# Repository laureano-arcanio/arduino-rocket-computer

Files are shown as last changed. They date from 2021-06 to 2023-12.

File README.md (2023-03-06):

# Arduino Rocket Flight Computer
An Arduino based hardware and software for model rockets recovery and logging system.

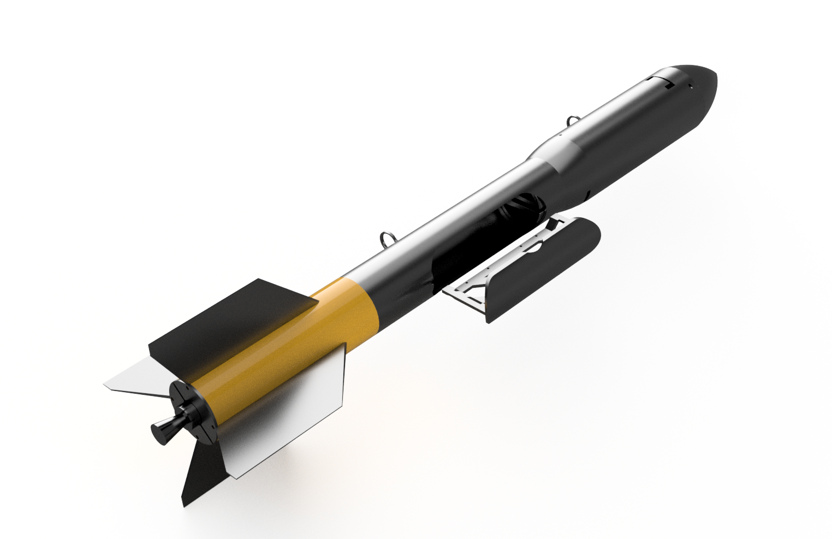
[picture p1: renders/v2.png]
Model 1


## How it works ?
Altitude is measured using a Presion BMP180 Sensor. Data is passed through a Kalman filter and then apogee is detected after 3 consecutive altitude drops.
Logs are stored in a SD card as CSV format, with 1kb redced EEPROM storage as backup (204 rows of 5 bytes).

Parachute deployment is done using a 180º Servo motor

Check out the circuit [here](/schematics/protoboard.png) 

### Full Assembly
Full Assembly

### STL Files
Stl files
All body parts are printed with 1 wall, and 10% infill except for the payload area that needs supports for the servo mount. 

### The Team
The Team

## Check all our FLights and Log [here](https://github.com/laureano-arcanio/arduino-rocket-computer/blob/main/LOGS.md)

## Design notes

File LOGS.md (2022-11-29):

## Saturday, October 15th 2022 18:04pm
### First Rocket Flight
- **Date:** Saturday, October 15th 2022 18:04pm
- **Rocket version:** v46
- **Computer firmware:** Commit 24 #9e297cbeb49c01d56837683099e77f7d58b3c18b
- **Engine:** 18g KNSU (water re-cristalinization)
- **Status:** Partial success, rocket recovered safe. Data logs not stored

**Logs:**

Our first flight deployed parachute before apogee, due to an issue with flight computer executing Emergency mode right after liftoff. Anyways, we recovered the entire rocket without any damage.
[First Flight](https://www.youtube.com/watch?v=o5odCazfV4E)

## Saturday, October 15th 2022 18:04pm
### Second Rocket Flight
Same as before

## October 16th 2022 18:04pm
### Third Rocket Flight (Cancelled)
- **Date:** Sunday, October 16th 2022 18:04pm
- **Rocket version:** v46
- **Computer firmware:** Commit 24 #9e297cbeb49c01d56837683099e77f7d58b3c18b
- **Engine:** 18g KNSU (water re-cristalinization)
- **Status:** Cancelled due to low battery and wiring issue.

**Logs:**

Our battery compleately died. We struggle with some bad wiring for a long time beferohand. 

## Saturday, October 29th 2022 20:15pm
### Fourth Rocket flight
- **Date:** Saturday, October 29th 2022 20:15pm
- **Rocket version:** v48
- **Computer firmware:** Commit 38 ec74b0bc3eabf66b300b1d60ef9739c1b33f2775
- **Engine:** 18g KNSU (water re-cristalinization)
- **Status:** Failure. Engine failure, Computer failure. 

**Logs:**

We experienced several unknown issues, initially servo lock did not work. This overheated the servo and some wires burnt out. After several attemps, we manage to get computer to ready status, fired the rocket but engine failes at about 5-7 mts hight. Rocket recovered almost 100% safe except for a broken finn. None logs where stored, we figured out 180deg servos don't work well on edges. so we switched from 0 to 25 deg to 15 to 40.

## Wednesday, November 9 2022 17hs
### Fifth Rocket Flight
- **Date:** Wednesday, November 9 2022 17hs
- **Weather**: Sunny, Windy (10-15knots)
- **Rocket version:** v48
- **Computer firmware:** Commit 44 58a310a3b09a8df3bc02ff4712aa3345adc88105
- **Engine:** 18g KNSU (Nakka method, caramelization of fine powder grains)
- **Status:** Failure. Computer failure. Avionics totally destroyed, computer, parachute and engine recovered

**Logs:**

Our rocket flow perfectly, but parachute did not ejected. After landing, and some further investigation we figured out for some reason the computer switched to Liftoff status before liftoff (probably due to pression change, was a windy day). And due to launchpad conditions switched to landed after 3.5s. So the rocket flown with a computer in Landed status. We'll fix the liftoff condition to account for more meters (>5) and shorten EMERGENCY deploy time to fit this rocket motor. (4s)
[Fifth Flight](https://www.youtube.com/watch?v=9i5LRDVh-5M)

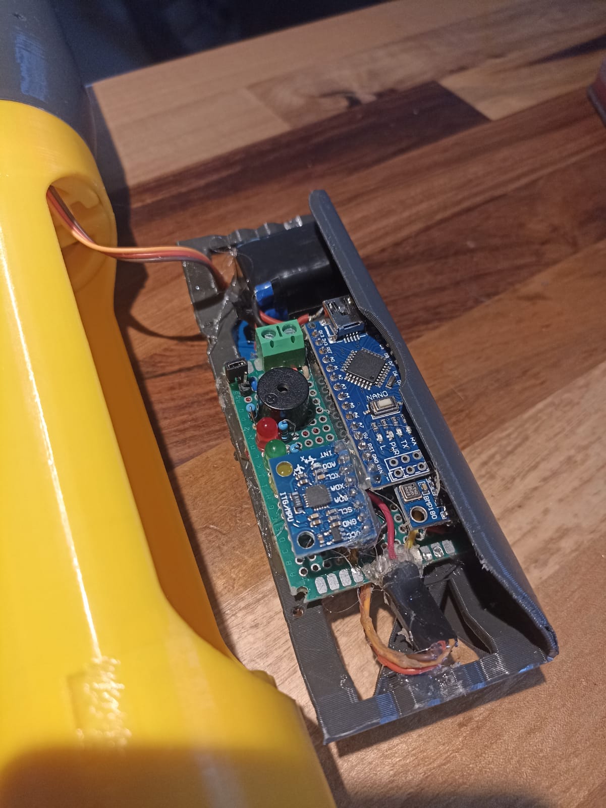
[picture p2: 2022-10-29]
images/Electronics_v1.jpeg

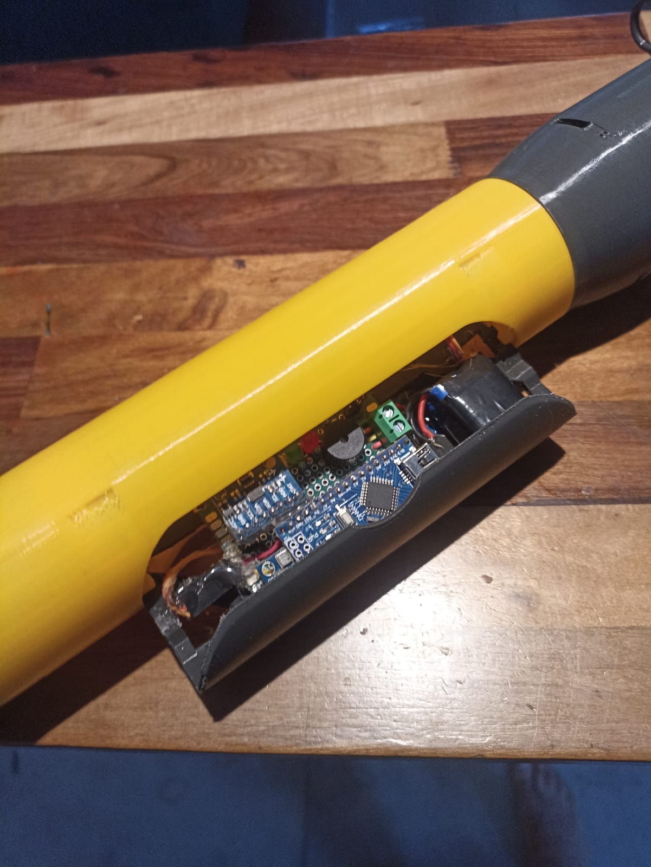
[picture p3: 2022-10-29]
images/Electronics_bay_v2.jpeg

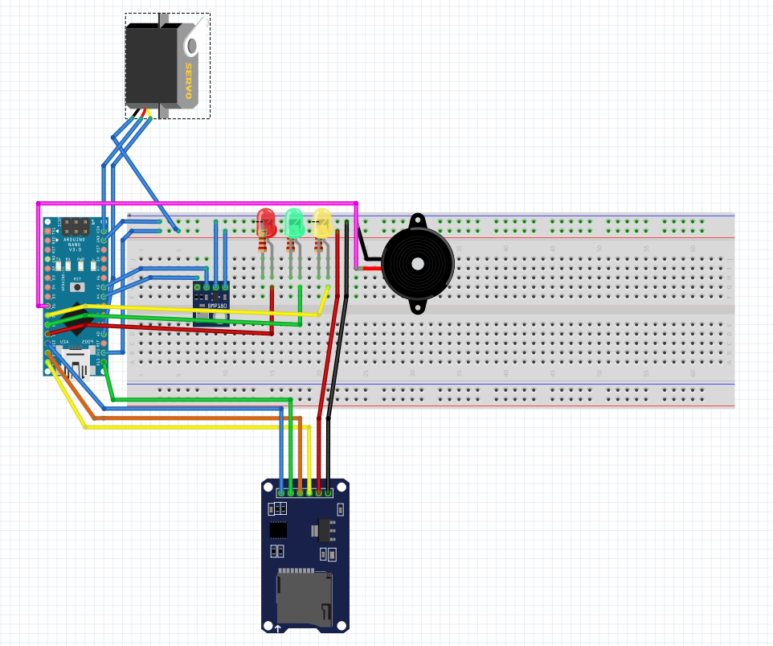
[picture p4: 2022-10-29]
schematics/protoboard.png

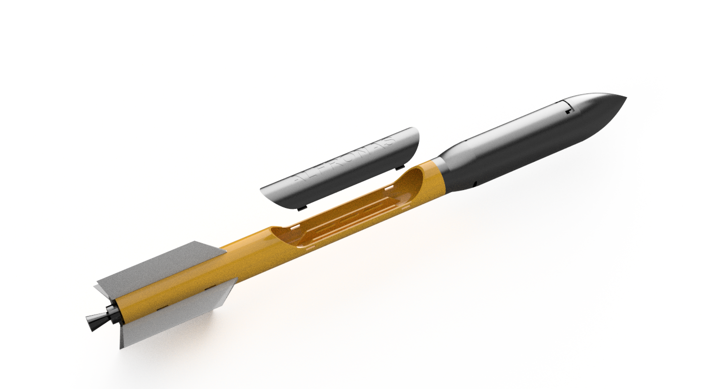
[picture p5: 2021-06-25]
renders/v1.png

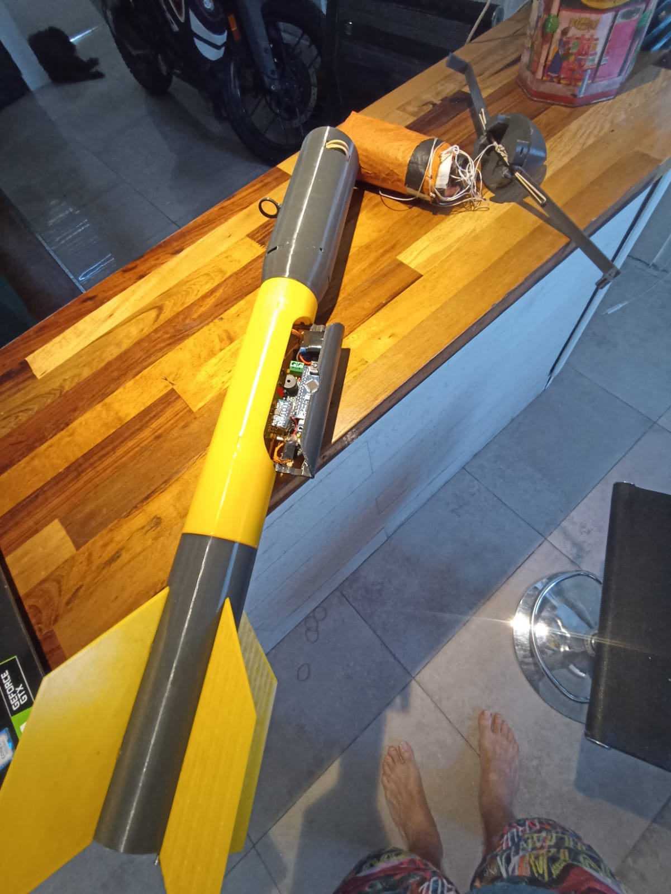
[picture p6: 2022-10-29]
images/Full_chute_deploy_v2.jpeg

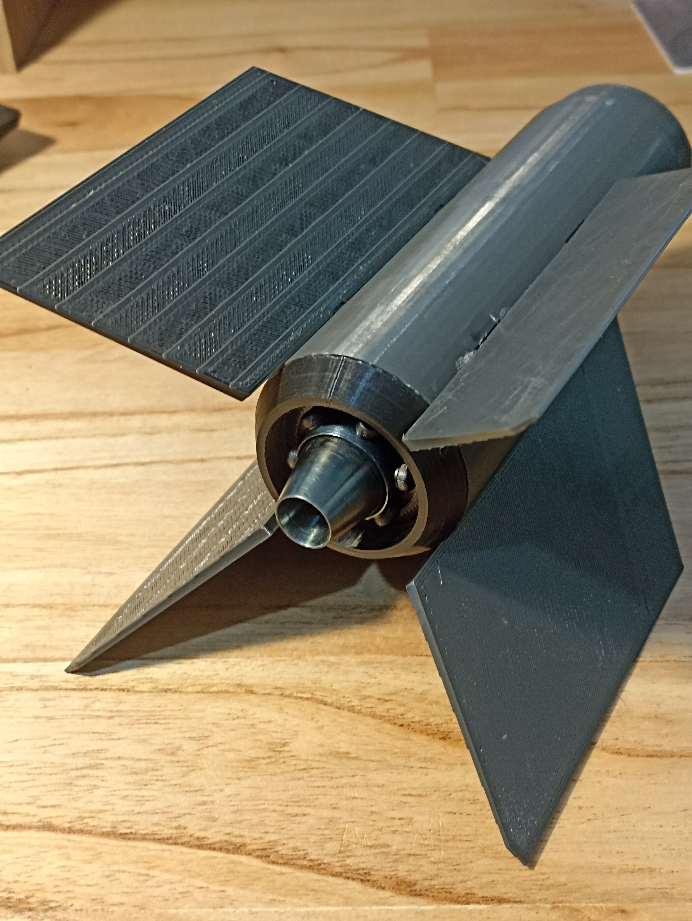
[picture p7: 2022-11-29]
images/E motor mounted.jpg

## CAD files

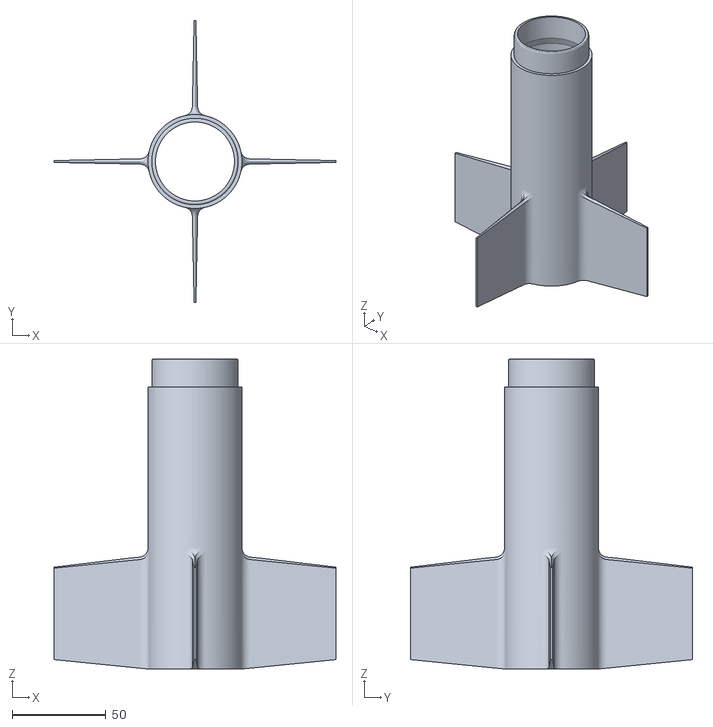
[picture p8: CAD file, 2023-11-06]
STLs/body_motor_section.stl
149.9 x 149.9 x 165.0

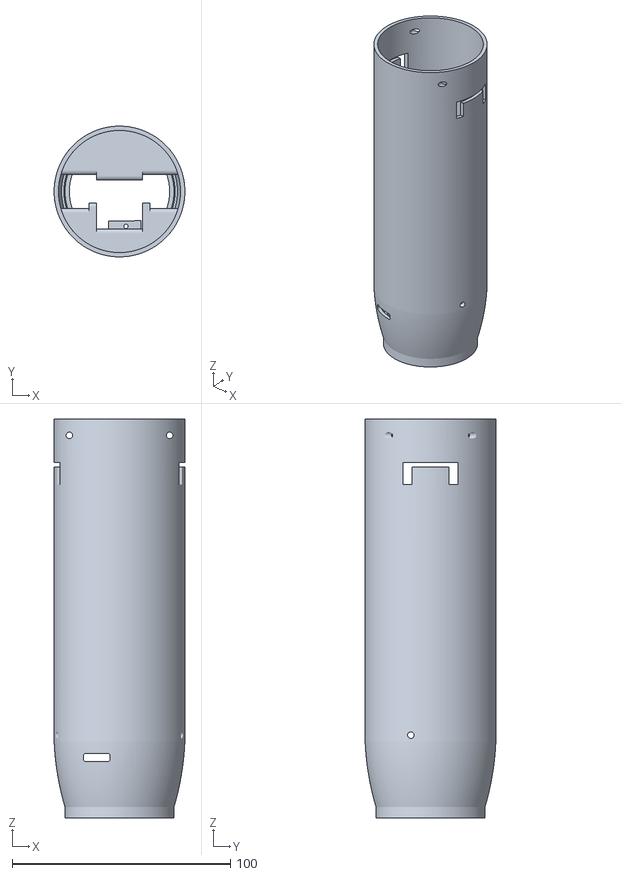
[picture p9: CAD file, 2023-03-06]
STLs/body_payload_area.stl
60.0 x 60.0 x 183.0

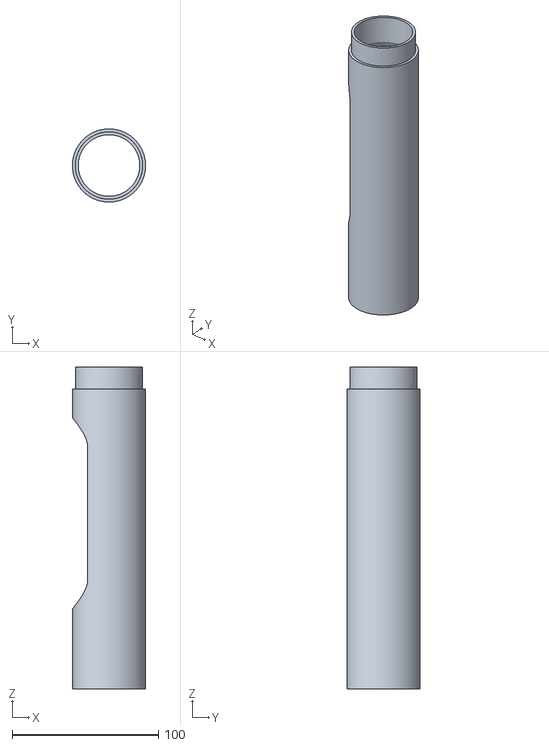
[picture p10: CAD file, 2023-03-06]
STLs/body_electronics_munt.stl
50.0 x 50.0 x 220.0

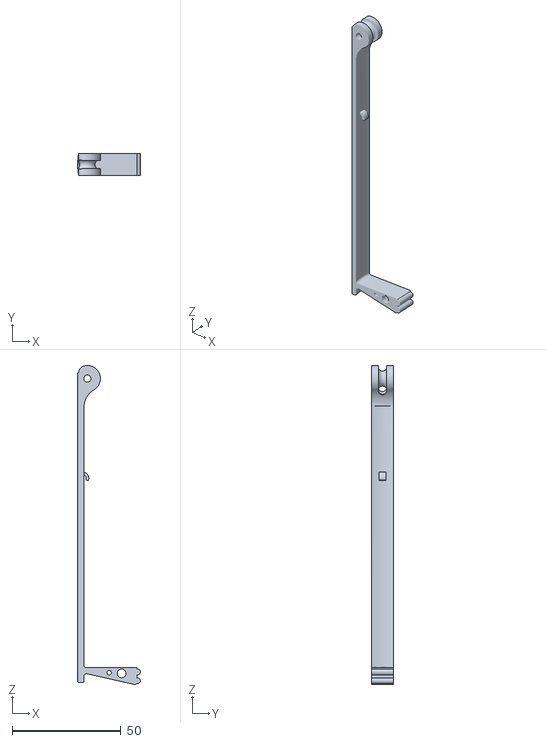
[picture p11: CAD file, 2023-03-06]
STLs/payload_release_arm_left.stl
28.9 x 10.0 x 146.4

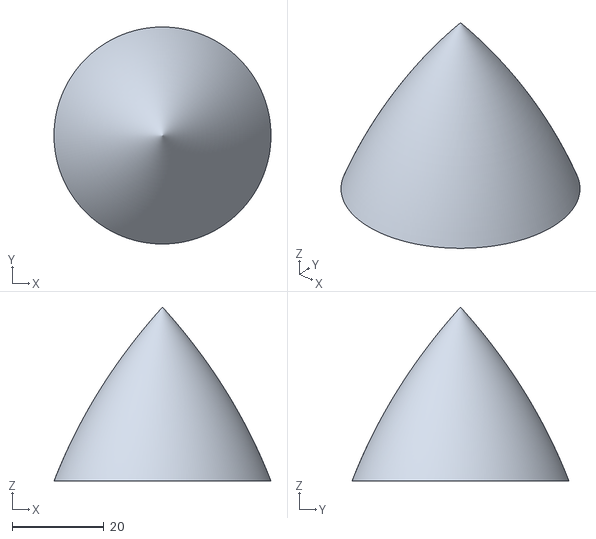
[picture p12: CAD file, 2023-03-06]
STLs/payload_release_nose_top.stl
47.4 x 47.4 x 38.0

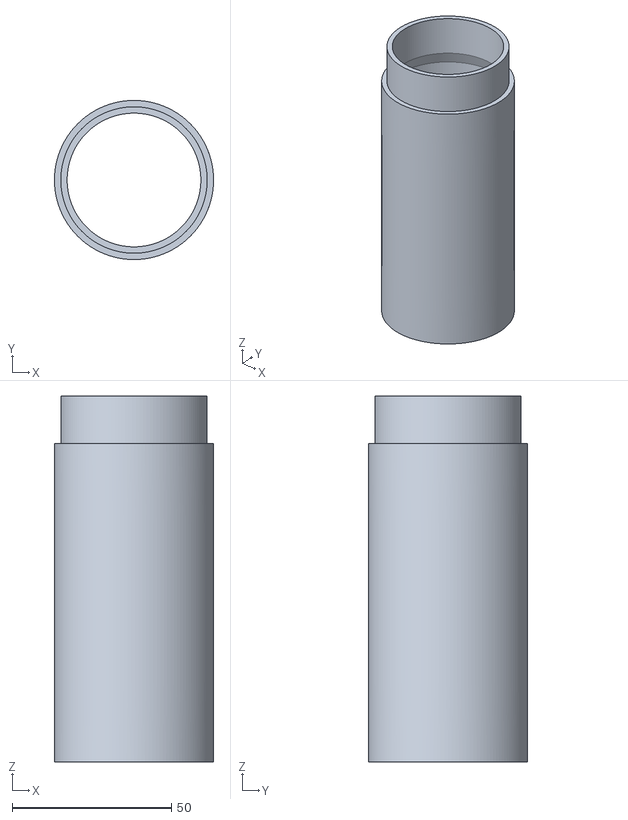
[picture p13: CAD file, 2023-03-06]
STLs/body_extension.stl
50.0 x 50.0 x 115.0

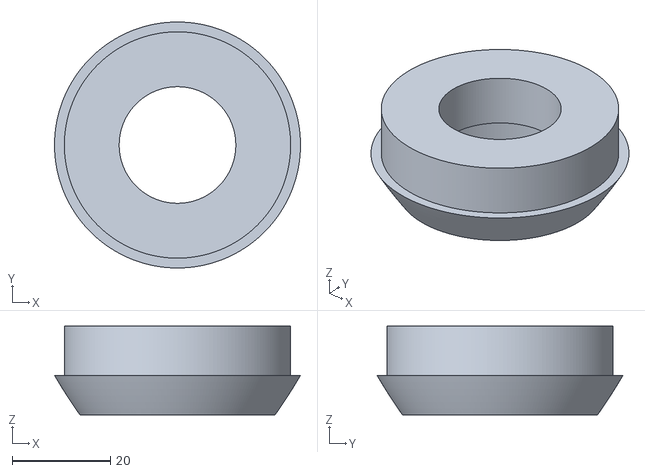
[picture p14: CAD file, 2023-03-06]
STLs/abs_motor_mount.stl
50.0 x 50.0 x 18.0

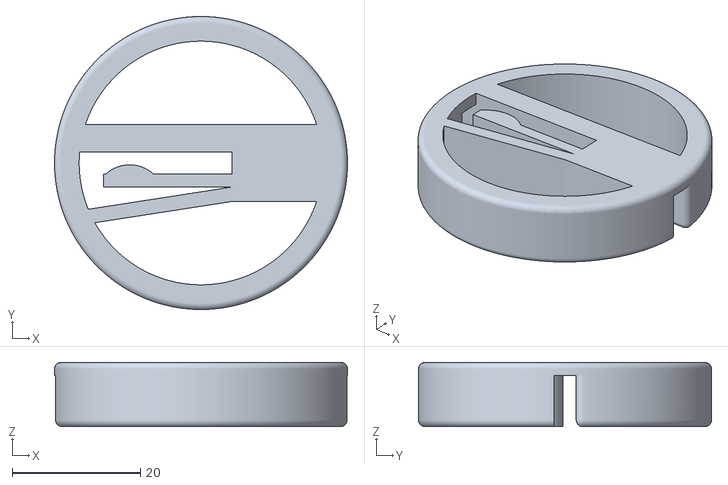
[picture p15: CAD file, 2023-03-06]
STLs/electronics_rack_guide_top.stl
45.7 x 45.7 x 10.0

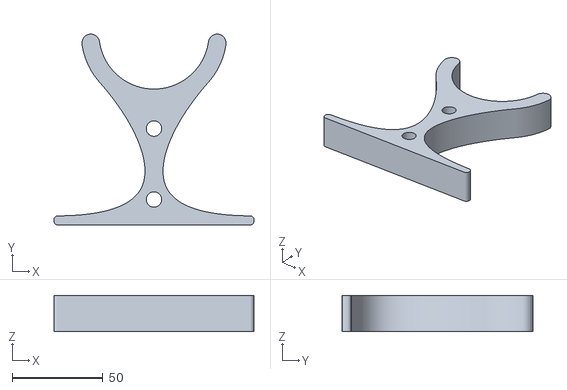
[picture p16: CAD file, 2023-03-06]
STLs/rocket_stand_base.stl
110.0 x 105.0 x 20.0

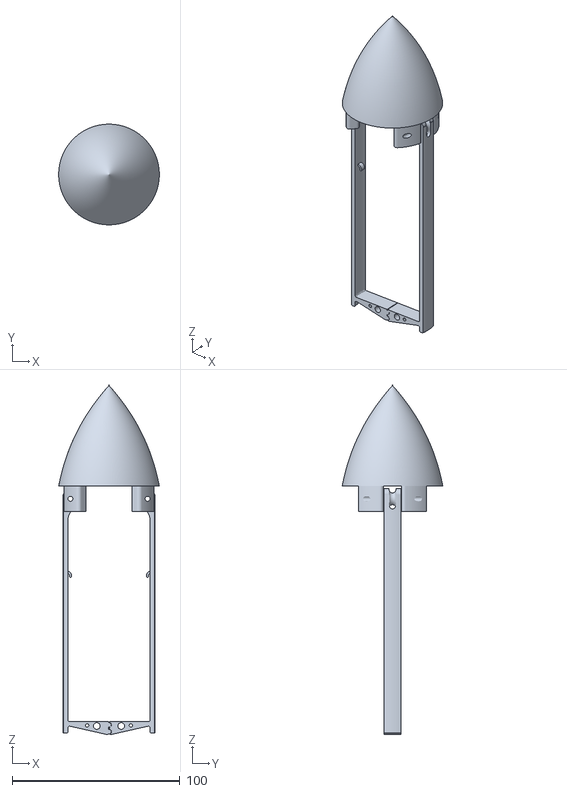
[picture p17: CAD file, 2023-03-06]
STLs/payload_release_arm_right.stl
60.0 x 60.0 x 207.9

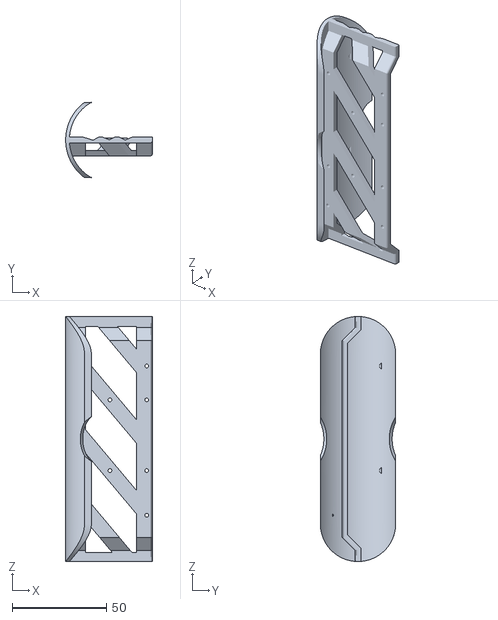
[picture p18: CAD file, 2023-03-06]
STLs/electronics_rack.stl
46.0 x 40.0 x 130.0

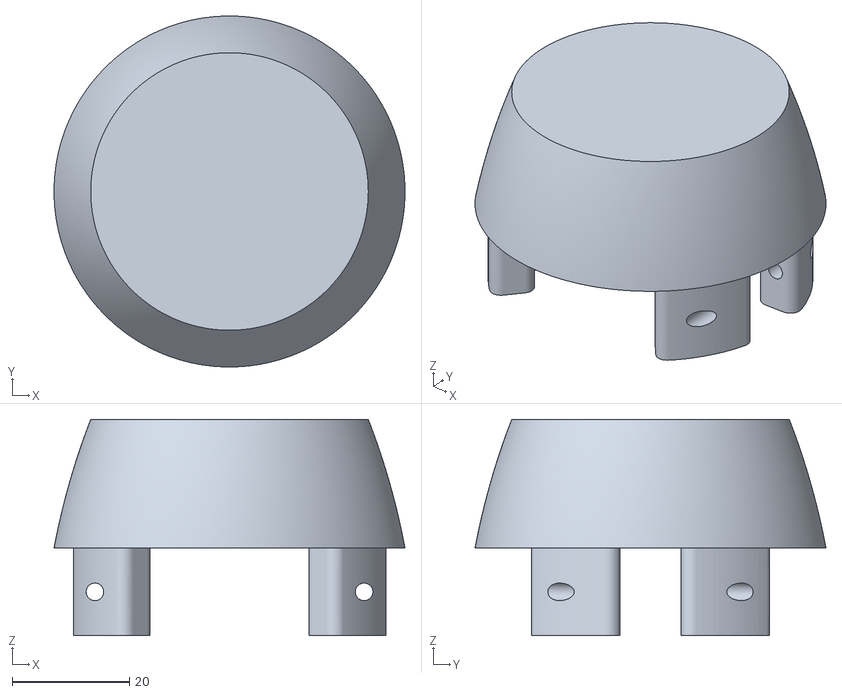
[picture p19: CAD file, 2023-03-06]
STLs/payload_release_nose_base.stl
60.0 x 60.0 x 37.0

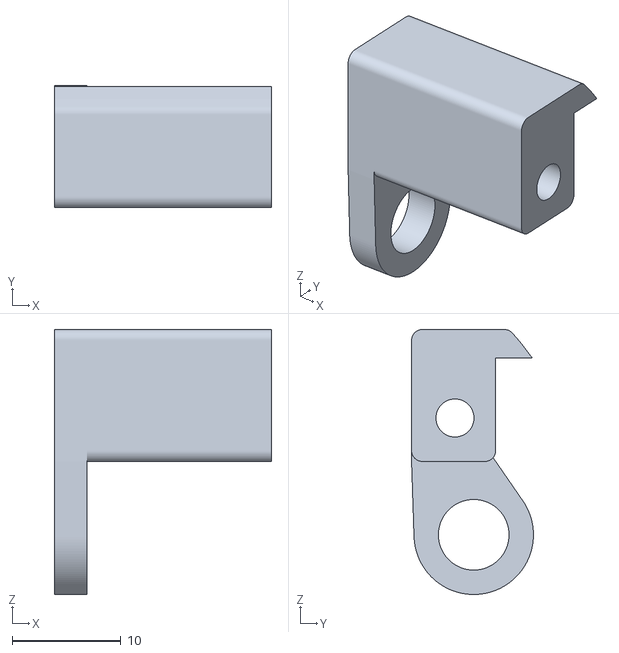
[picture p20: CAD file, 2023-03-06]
STLs/payload_release_pin.stl
20.0 x 11.2 x 24.4

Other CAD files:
STLs/electronics_rack_guide_bottom.stl

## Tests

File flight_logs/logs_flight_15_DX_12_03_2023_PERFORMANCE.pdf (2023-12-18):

## Rocket Flight Analisys

Rocket Mass): 0.41 kg
Max altitude: 250 Mts
Time at max altitude: 7.29 s Max Speed: 85.73 mts/s
Time at max speed: 1.07 s
Power flight time (s): 1.03 s
Max Acceleration: 167.3 mts/s^2 Time at max acceleration: 0.0 s Total Impulse: 35.2 Ns
Average descent speed: -9.57 mts/s

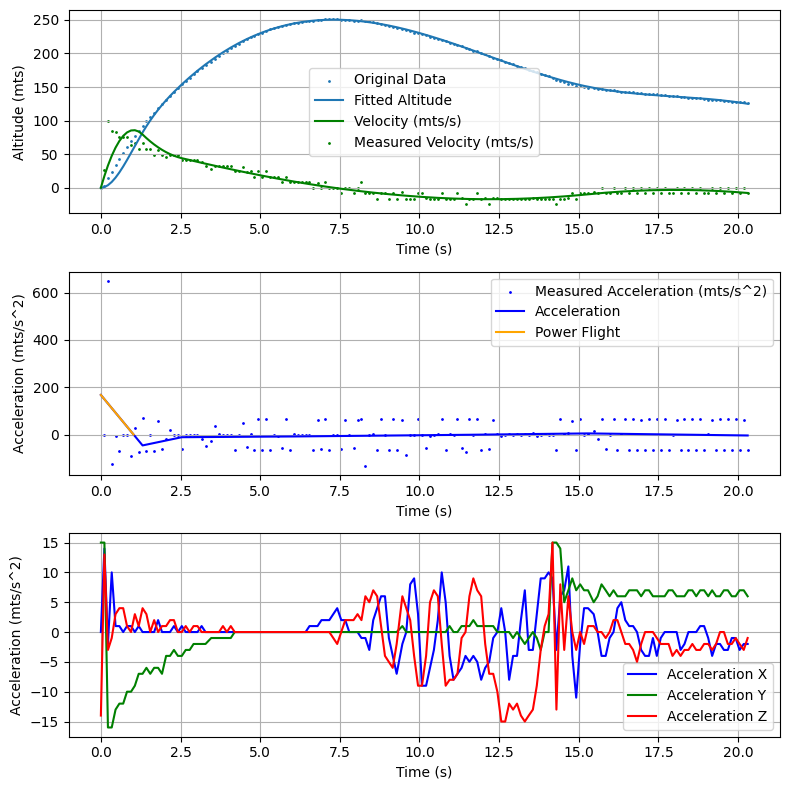
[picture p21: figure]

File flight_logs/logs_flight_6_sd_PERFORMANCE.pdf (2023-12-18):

## Rocket Flight Analisys

Rocket Mass): 0.41 kg
Max altitude: 42 Mts
Time at max altitude: 3.16 s Max Speed: 20.34 mts/s
Time at max speed: 1.55 s
Power flight time (s): 1.52 s
Max Acceleration: 26.77 mts/s^2 Time at max acceleration: 0.0 s Total Impulse: 8.34 Ns
Average descent speed: -2.38 mts/s

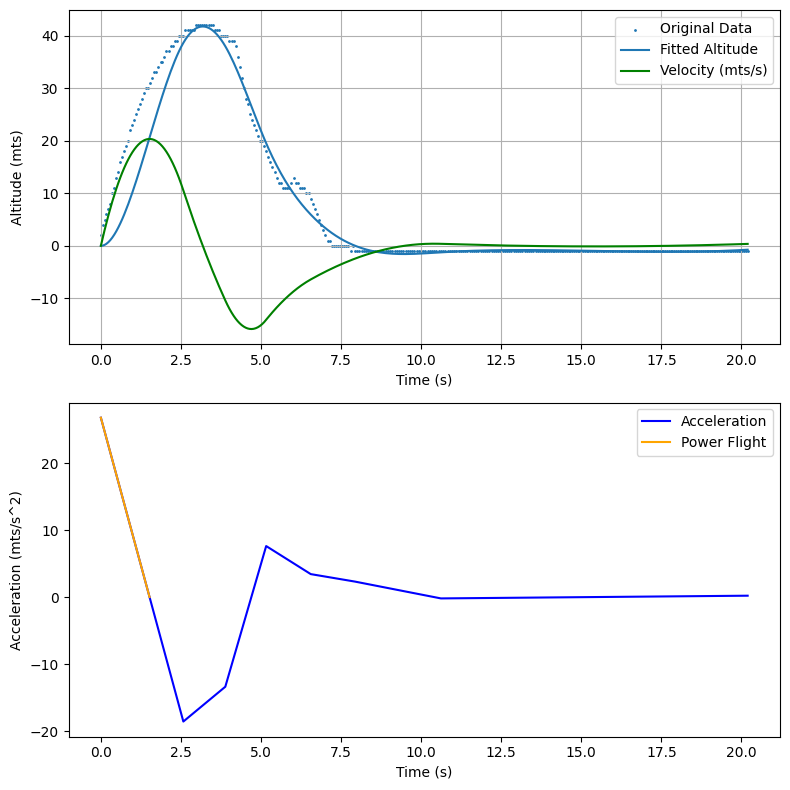
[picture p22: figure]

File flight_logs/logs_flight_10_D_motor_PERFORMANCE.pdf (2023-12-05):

## Rocket Flight Analisys

Rocket Mass): 0.41 kg
Max altitude: 137 Mts
Time at max altitude: 5.76 s Max Speed: 37.05 mts/s
Time at max speed: 2.8 s
Power flight time (s): 2.75 s
Max Acceleration: 26.96 mts/s^2 Time at max acceleration: 0.0 s Total Impulse: 15.2 Ns
Average descent speed: -4.56 mts/s

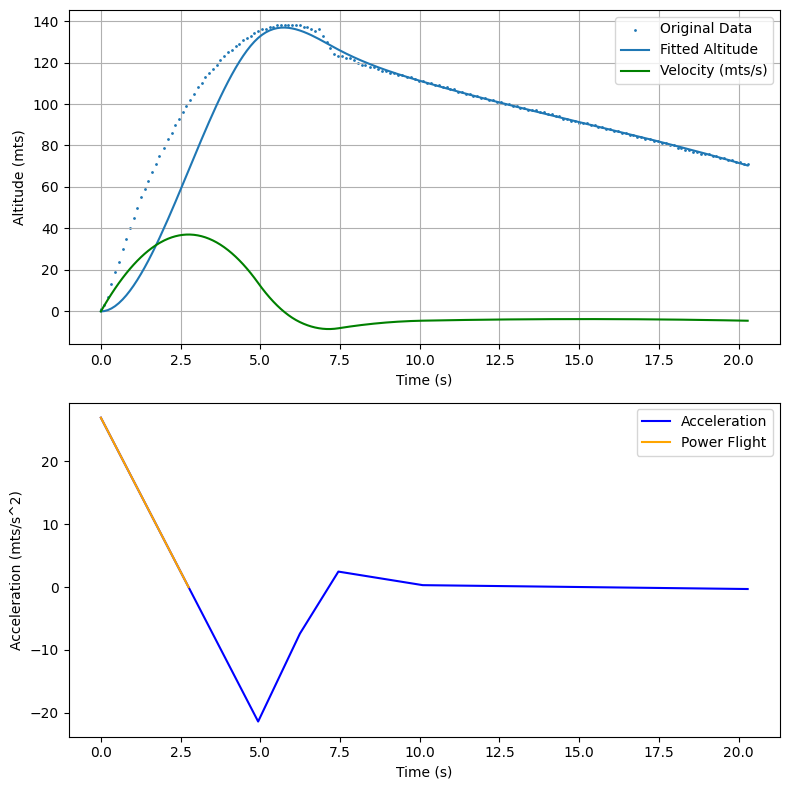
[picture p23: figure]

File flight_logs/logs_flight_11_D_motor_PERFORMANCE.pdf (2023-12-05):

## Rocket Flight Analisys

Rocket Mass): 0.41 kg
Max altitude: 139 Mts
Time at max altitude: 9.13 s Max Speed: 58.77 mts/s
Time at max speed: 0.81 s
Power flight time (s): 0.76 s
Max Acceleration: 161.53 mts/s^2 Time at max acceleration: 0.0 s Total Impulse: 24.15 Ns
Average descent speed: -6.49 mts/s

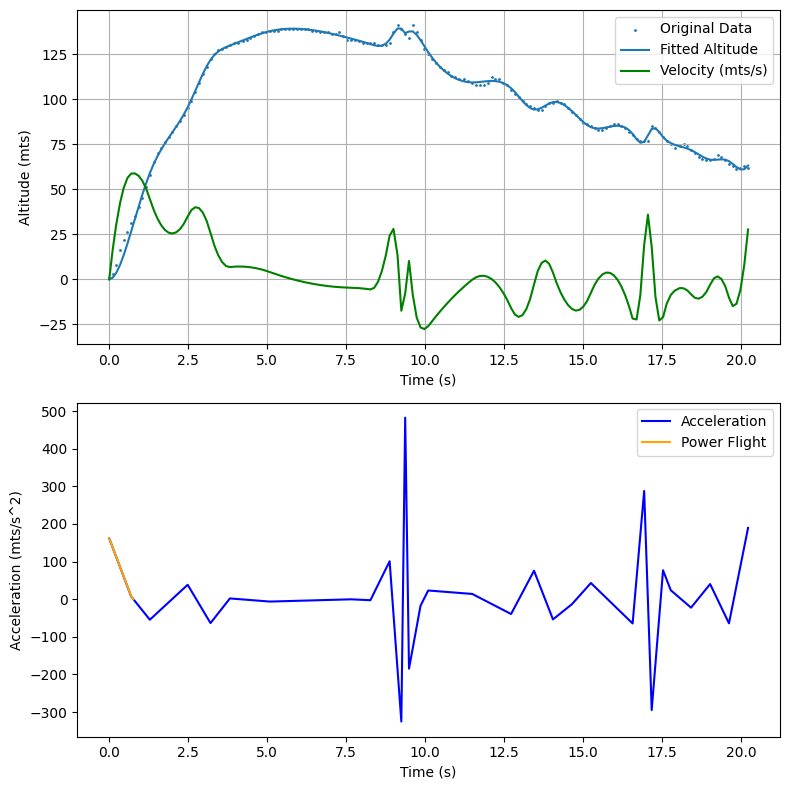
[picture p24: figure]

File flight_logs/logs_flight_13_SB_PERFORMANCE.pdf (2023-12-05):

## Rocket Flicht Analisys

Rocket Mass): 0.41 kg
Max altitude: 177 Mts
Time at max altitude: 6.43 s Max Speed: 67.89 mts/s
Time at max speed: 0.49 s
Power flight time (s): 0.47 s
Max Acceleration: 292.23 mts/s^2 Time at max acceleration: 0.0 s Total Impulse: 27.89 Ns
Average descent speed: -4.19 mts/s

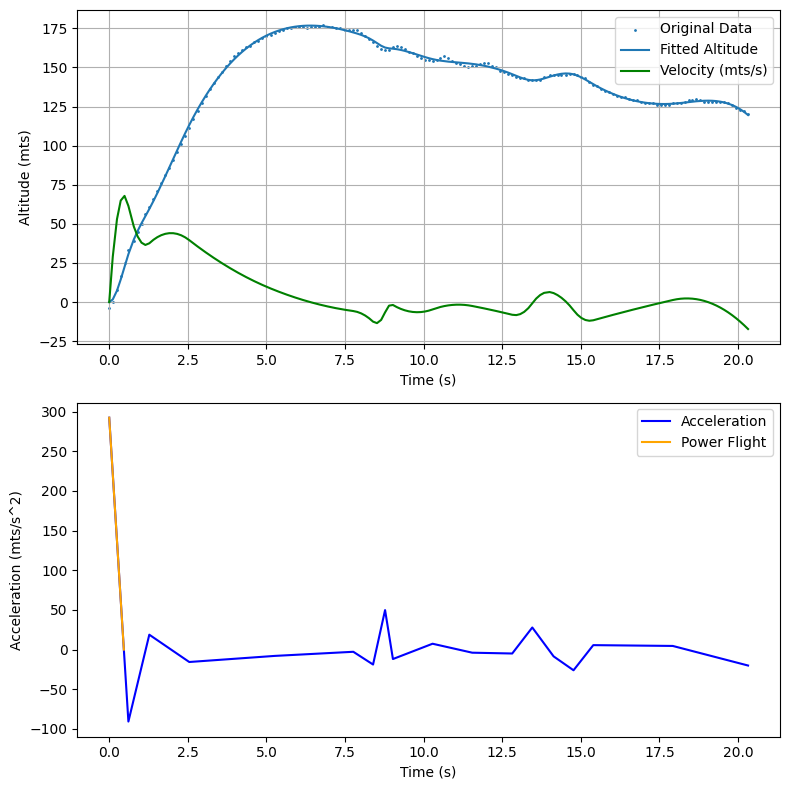
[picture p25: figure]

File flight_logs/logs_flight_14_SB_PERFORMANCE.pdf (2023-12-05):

## Rocket Flicht Analisys

Rocket Mass): 0.41 kg
Max altitude: 193 Mts
Time at max altitude: 6.58 s Max Speed: 56.46 mts/s
Time at max speed: 1.88 s
Power flight time (s): 1.9 s
Max Acceleration: 59.37 mts/s^2 Time at max acceleration: 0.0 s Total Impulse: 23.15 Ns
Average descent speed: -4.02 mts/s

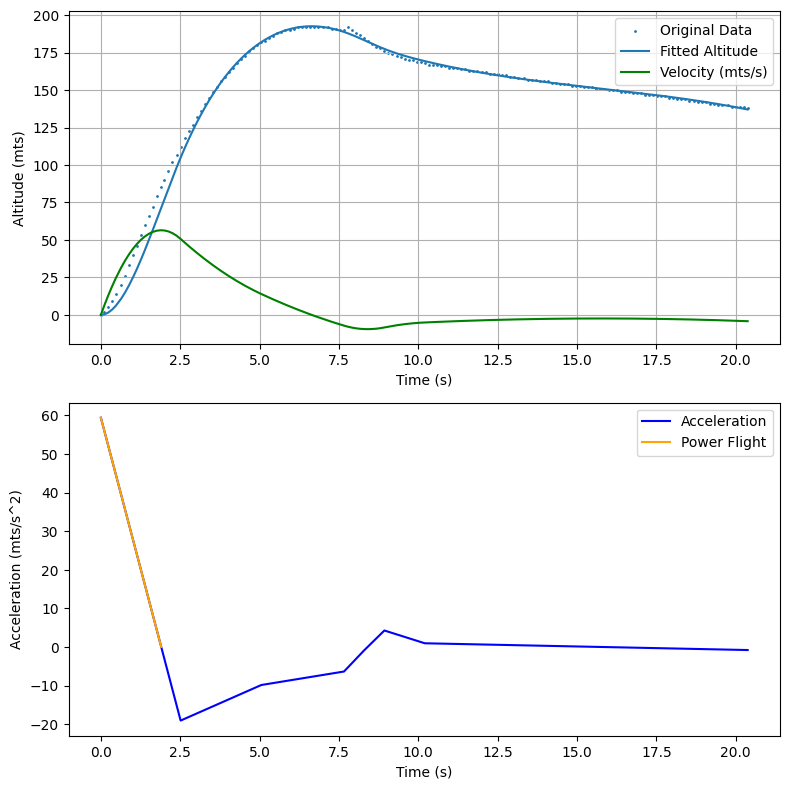
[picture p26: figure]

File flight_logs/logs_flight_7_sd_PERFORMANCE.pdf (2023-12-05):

## Rocket Flight Analisys

Rocket Mass): 0.41 kg
Max altitude: 32 Mts
Time at max altitude: 2.9 s Max Speed: 16.85 mts/s
Time at max speed: 1.4 s
Power flight time (s): 1.42 s
Max Acceleration: 23.78 mts/s^2 Time at max acceleration: 0.0 s Total Impulse: 6.91 Ns
Average descent speed: -1.78 mts/s

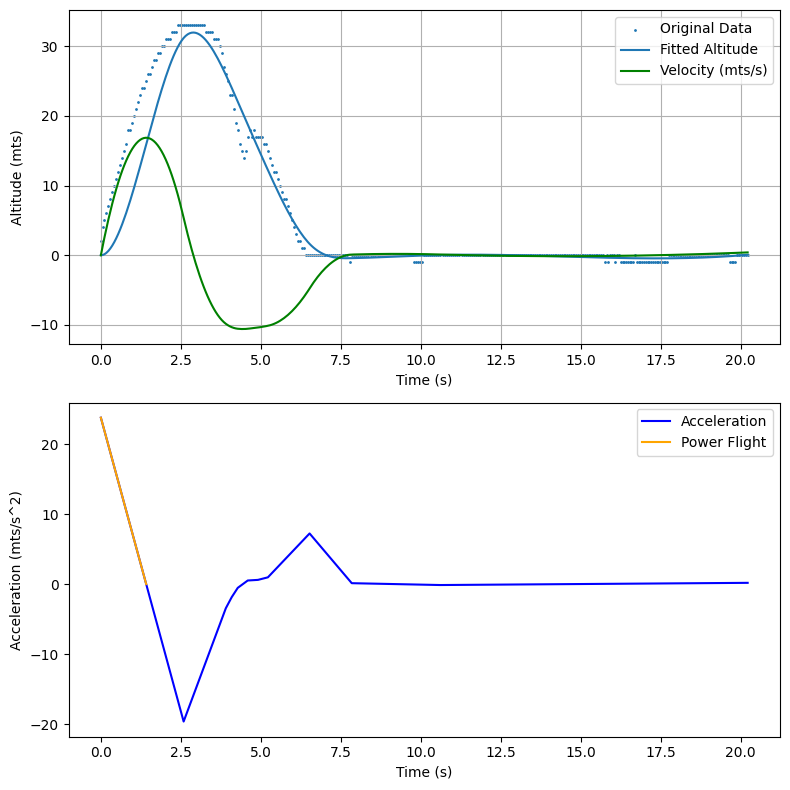
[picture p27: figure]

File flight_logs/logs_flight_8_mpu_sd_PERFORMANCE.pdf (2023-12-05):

## Rocket Flight Analisys

Rocket Mass): 0.41 kg
Max altitude: 44 Mts
Time at max altitude: 3.36 s Max Speed: 20.17 mts/s
Time at max speed: 1.61 s
Power flight time (s): 1.63 s Max Acceleration: 24.7 mts/s^2 Time at max acceleration: 0.0 s Total Impulse: 8.27 Ns
Average descent speed: -2.47 mts/s

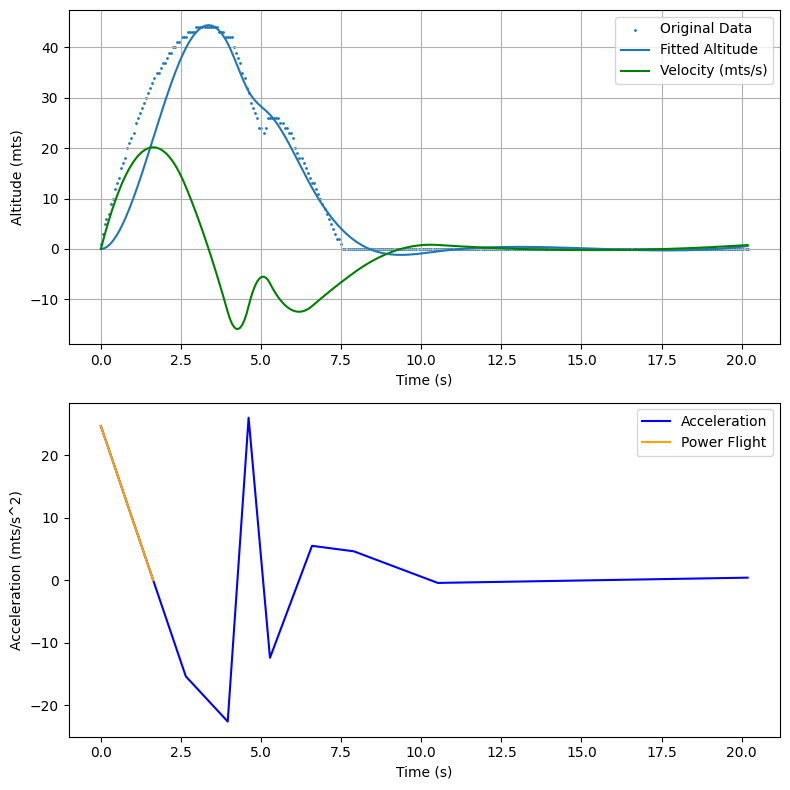
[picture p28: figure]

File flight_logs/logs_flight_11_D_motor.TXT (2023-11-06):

Ms	Code	A0	CA	MA	T	AX	AY	AZ	GX	GY	GZ
0	20	0.00	0	0.60	29.20	0	-8	0	-136	-821	-6	
106	20	0.00	0	1.83	29.20	0	-7	0	-302	-15	-12	
210	20	0.00	1	1.39	29.20	0	-7	0	-268	-554	27	
317	20	0.00	1	1.22	29.20	0	-7	0	-178	-293	-111	
422	20	0.00	1	1.48	29.20	0	-8	0	-177	-308	-31	
529	20	0.00	1	1.30	29.20	0	-8	0	-276	-439	13	
635	20	0.00	1	1.13	29.30	0	-8	0	-285	-522	-37	
748	20	0.00	1	1.48	29.30	0	-7	0	-296	167	105	
852	20	0.00	1	2.00	29.20	0	-8	0	-120	-714	-183	
959	20	0.00	1	1.83	29.20	0	-8	0	-347	-35	136	
1064	20	0.00	1	1.30	29.20	0	-8	0	-264	609	177	
1172	20	0.00	1	2.17	29.20	0	-8	0	-236	-327	-156	
1279	20	0.00	1	1.74	29.30	0	-8	0	-411	-593	-80	
1386	20	0.00	1	1.91	29.30	0	-7	0	-297	-488	-83	
1493	20	0.00	1	2.17	29.30	0	-8	-1	-358	-2049	78	
1600	20	0.00	1	1.74	29.30	0	-7	0	-452	-249	-67	
1707	20	0.00	1	2.00	29.30	0	-8	0	-152	-352	-10	
1815	20	0.00	1	1.65	29.30	0	-8	0	-121	-197	-163	
1928	20	0.00	1	1.56	29.30	0	-8	0	-367	-662	-70	
2034	20	0.00	1	2.00	29.30	0	-8	0	-274	70	127	
2141	20	0.00	1	1.74	29.30	0	-8	0	-210	-147	84	
2249	20	0.00	1	1.65	29.30	0	-8	0	-346	-605	-160	
2355	20	0.00	1	2.52	29.30	0	-8	0	-193	-268	-139	
2463	20	0.00	1	1.48	29.30	0	-7	0	-235	-156	96	
2569	20	0.00	1	1.65	29.30	0	-8	0	-326	-138	-29	
2677	20	0.00	1	1.91	29.30	0	-8	0	-324	-514	-146	
2784	20	0.00	1	1.91	29.30	0	-8	0	-46	-321	-78	
2891	20	0.00	1	1.13	29.30	0	-8	0	-226	-408	131	
2999	20	0.00	1	1.74	29.30	0	-8	0	-437	-132	67	
3112	20	0.00	1	1.22	29.30	0	-8	0	-175	-295	-111	
3219	20	0.00	1	1.74	29.30	0	-7	0	-226	19	-75	
3325	20	0.00	1	1.13	29.30	0	-8	0	-393	53	196	
3433	20	0.00	1	1.65	29.30	0	-8	0	-375	228	166	
3539	20	0.00	1	1.30	29.30	0	-8	0	-152	-406	-128	
3647	20	0.00	1	1.48	29.30	0	-8	0	-256	-511	-208	
3754	20	0.00	1	1.39	29.30	0	-7	0	-296	-315	3	
3861	20	0.00	1	1.83	29.30	0	-8	0	-202	75	110	
3968	20	0.00	1	1.39	29.30	0	-8	0	-284	-179	-25	
4076	20	0.00	1	1.22	29.30	0	-8	0	-342	-56	-94	
4182	20	0.00	1	0.34	29.40	-1	-8	0	-220	-160	119	
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

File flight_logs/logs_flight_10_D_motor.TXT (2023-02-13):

Ms	Code	A0	CA	MA	T	AX	AY	AZ	GX	GY	GZ
0	20	0.00	0	-0.51	27.40	0	-8	0	-486	-1151	92	
123	20	0.00	0	-0.25	27.40	0	-8	0	-263	-312	7	
227	20	0.00	0	-0.25	27.50	0	-8	0	-243	-194	26	
334	20	0.00	0	-0.16	27.50	0	-8	0	-286	17	-38	
441	20	0.00	0	-0.25	27.50	0	-8	0	-238	-25	11	
548	20	0.00	0	0.11	27.50	0	-8	0	-132	511	47	
655	20	0.00	0	0.02	27.50	-1	-4	0	-148	1356	-66	
760	20	0.00	0	-0.07	27.50	0	-8	0	-159	-217	33	
867	20	0.00	0	0.20	27.50	0	-8	0	-52	1188	-238	
973	20	0.00	0	-0.51	27.50	0	-8	0	7	-1045	-80	
1081	20	0.00	0	0.54	27.50	0	-8	0	-321	-392	8	
1194	20	0.00	0	-0.16	27.50	0	-8	0	-549	3642	16	
1299	20	0.00	0	0.28	27.50	0	-8	0	-224	1180	-180	
1406	20	0.00	0	-0.33	27.50	0	-7	0	-138	-217	-32	
1514	20	0.00	0	-0.60	27.50	0	-8	0	-419	351	58	
1622	20	0.00	0	-0.16	27.50	0	-8	0	-272	-323	-40	
1731	20	0.00	0	-0.07	27.50	0	-8	0	-106	-565	-34	
1838	20	0.00	0	-0.42	27.50	0	-8	0	-229	-208	26	
1947	20	0.00	0	-0.42	27.50	0	-8	0	-432	131	-16	
2056	20	0.00	0	-0.16	27.50	0	-8	0	-225	-305	-37	
2163	20	0.00	0	-0.42	27.50	0	-8	0	-87	-578	10	
2278	20	0.00	0	0.11	27.50	0	-8	0	-264	-87	-18	
2382	20	0.00	0	0.11	27.50	0	-8	0	-361	30	-45	
2489	20	0.00	0	-0.25	27.50	0	-8	0	-175	-401	27	
2597	20	0.00	0	0.11	27.50	0	-8	0	-152	-467	-32	
2704	20	0.00	0	0.20	27.50	0	-7	0	-301	-172	-24	
2811	20	0.00	0	-0.51	27.50	0	-8	0	-348	-109	14	
2920	20	0.00	0	-0.42	27.50	0	-8	0	-159	-469	-24	
3027	20	0.00	0	-0.25	27.50	0	-8	0	-177	-454	-18	
3136	20	0.00	0	-0.16	27.50	0	-8	0	-345	-114	0	
3243	20	0.00	0	-0.16	27.50	0	-8	0	-295	-165	-23	
3353	20	0.00	0	-0.33	27.50	0	-8	0	-115	-492	-22	
3503	20	0.00	0	0.20	27.50	0	-8	0	-313	-166	-22	
3608	20	0.00	0	-0.07	27.50	0	-8	0	-323	-65	-10	
3715	20	0.00	0	-0.25	27.50	0	-8	0	-190	-406	6	
3824	20	0.00	0	-0.07	27.50	0	-8	0	-160	-429	-10	
3933	20	0.00	0	0.02	27.50	0	-8	0	-319	-168	-21	
4039	20	0.00	0	-0.07	27.50	0	-8	0	-288	-141	-21	
4148	20	0.00	0	-0.25	27.50	0	-8	0	-147	-405	37	
4255	20	0.00	0	0.02	27.50	0	-8	0	-211	-320	-20	
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

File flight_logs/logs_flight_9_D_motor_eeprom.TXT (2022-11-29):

15161	L	7
15168	L	13
15175	L	18
15182	L	22
15190	L	26
15197	L	30
15203	L	33
15210	L	36
15217	L	39
15224	L	41
15231	L	44
15238	L	48
15245	L	51
15252	L	53
15259	L	56
15266	L	59
15273	L	62
15280	L	64
15287	L	66
15294	L	69
15301	L	71
15308	L	74
15315	L	76
15322	L	78
15329	L	81
15336	L	83
15343	L	85
15350	L	87
15357	L	89
15364	L	92
15371	L	94
15378	L	96
15385	L	98
15392	L	99
15399	L	101
15406	L	103
15413	L	105
15420	L	106
15427	L	108
15434	L	109
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

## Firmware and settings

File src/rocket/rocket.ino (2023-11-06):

/*

  Arduino Rocket Computer

  Authors:
  -------------------
    Laureano Arcanio
    Jeremias Giorgi
    Martiniano Arcanio

  Contact Info
  -------------------
    laureano.arcanio@gmail.com

    Based on work from
    Boris du Reau / https://github.com/bdureau

*/
#include <EEPROM.h>
#include <Wire.h>
#include <SPI.h>
#include <SD.h>
#include <Adafruit_BMP085.h>
#include <MPU6050.h>
#include <Servo.h>

#define SERIAL_DEBUG true

Servo servo;
MPU6050 mpu;
Adafruit_BMP085 bmp;
int ax, ay, az, gx, gy, gz;

File root;

boolean useMPUData = true;
boolean allOn = true;
String filename;
float P0;
float initialAltitude = 0;
int previousLoopAltitude = 0;
int currentLoopAltitude = 0;
float rawAltitude = 0;
float rawTemp = 0;
boolean hasHeaders = false;


unsigned long millisAtLiftoff = 0;
unsigned long millisFromLastBlink = 0;
unsigned long millisAtCurrentLoop = 0;
unsigned long millisAtLoopStart = 0;
bool apogeeHasFired = false;

// Time interval to check for landed condition
const unsigned short LANDED_THRESHOLD = 3;
unsigned short millisFromLastLandedCheck = 0;

unsigned short landedCheckCounts = LANDED_THRESHOLD;


// Eeprom variables
unsigned short eepromAvalableBytes = 1024;

// Status
const unsigned short STATUS_READY = 20;
const unsigned short STATUS_LIFTOFF = 40;
const unsigned short STATUS_APOGEE = 60;
const unsigned short STATUS_EMERGENCY_DEPLOY = 70;
const unsigned short STATUS_LANDED = 80;
unsigned short status = STATUS_READY;
// 1x Errors
// 10 = SD Error
// 11 = BMP Error
// 12 = MPU

// 20 = Ready
// 40 = Lisftoff
// 60 = Apogee
// 80 = Landed

// Landed threshold
const unsigned short LIFTOFF_THRESHOLD = 5;
// Security deploy time
// D motor of around 15Ns
//const unsigned int SECURITY_DEPLOYMENT_TIME = 4500; // Total flight for the current motor aprox 6.5 seconds

// E motor of around 35Ns
const unsigned int SECURITY_DEPLOYMENT_TIME = 12000;

// consecutive measures < apogee to run before apogee confirmation
const unsigned short APOGEE_THRESHOLD = 2;
unsigned int consecutiveAltitudeDrop = APOGEE_THRESHOLD;

// Pin Out
const unsigned int redLed = 9;
const unsigned int greenLed = 8;
const unsigned int blueLed = 7;
const unsigned int intLed = 13;
const int unsigned pinApogee = A0;
const int unsigned buzzer = 6;

void statusMonitor()
{
  if (allOn == true)
  {
    allOn = false;
    if (status == STATUS_READY)
    {
      digitalWrite(greenLed, HIGH);
    }
    if (status == STATUS_LIFTOFF)
    {
      digitalWrite(blueLed, HIGH);
    }
    if (status == STATUS_APOGEE)
    {
      digitalWrite(blueLed, HIGH);
      digitalWrite(greenLed, HIGH);
    }
    if (status == STATUS_LANDED)
    {
      digitalWrite(redLed, HIGH);
      digitalWrite(blueLed, HIGH);
      digitalWrite(greenLed, HIGH);
      tone(buzzer, 880);
    }
    if (status == STATUS_EMERGENCY_DEPLOY)
    {
      digitalWrite(redLed, HIGH);
    }

    if (status < 20)
    {
      if (status == 10)
      {
        digitalWrite(redLed, HIGH);
        digitalWrite(greenLed, HIGH);
      }
      if (status == 11)
      {
        digitalWrite(redLed, HIGH);
        digitalWrite(blueLed, HIGH);
      }
      // if (status == 12 ) {
      //   digitalWrite(LED_BUILTIN, HIGH);
      // }
      tone(buzzer, 880);
    }
  }
  else
  {
    allOn = true;
    digitalWrite(greenLed, LOW);
    digitalWrite(blueLed, LOW);
    digitalWrite(redLed, LOW);
    digitalWrite(intLed, LOW);
    noTone(buzzer);
  }
}

String getFileName(File dir, int numTabs)
{
  unsigned int fileCount = 1;
  while (true)
  {
    File entry = dir.openNextFile();
    if (!entry)
    {
      break;
    }
    fileCount++;
    entry.close();
  }
  return "LOGS_" + String(fileCount) + ".txt";
}

void sdDataLogger()
{
  if (useMPUData == true)
  {
    mpu.getAcceleration(&ax, &ay, &az);
    mpu.getRotation(&gx, &gy, &gz);
  }

  File dataFile = SD.open(filename, FILE_WRITE);
  if (dataFile)
  {
    if (hasHeaders == false)
    {
      // CSV format:
      // Millis from init, Status, Initial Altitude, Current Altitude (by kalman), Raw Altitude measurement, Acc X, Acc Y, Acc Z, Gyro X, Gyro Y, Giro Z
      dataFile.println("Ms\tCode\tA0\tCA\tMA\tT\tAX\tAY\tAZ\tGX\tGY\tGZ");
      hasHeaders = true;
    }
    dataFile.print(millisAtCurrentLoop);
    dataFile.print("\t");
    dataFile.print(status);
    dataFile.print("\t");
    dataFile.print(initialAltitude);
    dataFile.print("\t");
    dataFile.print(currentLoopAltitude);
    dataFile.print("\t");
    dataFile.print(rawAltitude);
    dataFile.print("\t");
    dataFile.print(rawTemp);
    dataFile.print("\t");
    dataFile.print(ax / 2048);
    dataFile.print("\t");
    dataFile.print(ay / 2048);
    dataFile.print("\t");
    dataFile.print(az / 2048);
    dataFile.print("\t");
    dataFile.print(gx);
    dataFile.print("\t");
    dataFile.print(gy);
    dataFile.print("\t");
    dataFile.print(gz);
    dataFile.print("\t");
    dataFile.print("\n");
    dataFile.close();
  }
}

void writeIntIntoEEPROM(int address, int number)
{ 
  EEPROM.update(address, number >> 8);
  EEPROM.update(address + 1, number & 0xFF);
}

int readIntFromEEPROM(int address)
{
  byte byte1 = EEPROM.read(address);
  byte byte2 = EEPROM.read(address + 1);
  return (byte1 << 8) + byte2;
}


void eepromDataLogger() {
  // Log flight data using 5 bytes per row
  // Timestamp(int 2 bytes) - Status (char 1 byte) - Altitude (int 2 bytes)

  if (eepromAvalableBytes >= 5) {
    unsigned short currentEepromAddress = 1024 - eepromAvalableBytes;
    writeIntIntoEEPROM(currentEepromAddress, millisAtCurrentLoop / 10); // Addr n+0, n+1)
    if (status == 40) { // STATUS_LIFTOFF
      EEPROM.update(currentEepromAddress + 2, 'L'); // Addr n+2)
    } else if (status == 60) { // STATUS_APOGEE
      EEPROM.update(currentEepromAddress + 2, 'A'); // Addr n+2)
    } else if (status == 70) { // STATUS_EMERGENCY_DEPLOY
      EEPROM.update(currentEepromAddress + 2, 'E'); // Addr n+2)
    } else { // ANY OTHER 
      EEPROM.update(currentEepromAddress + 2, 'X'); // Addr n+2)
    }
    
    writeIntIntoEEPROM(currentEepromAddress + 3, currentLoopAltitude ); // Addr n+3, n+4)
    eepromAvalableBytes -= 5;
  }
}
#if SERIAL_DEBUG
void eepromDataReader() {
  for (int i = 0; i<= 1024; i+=5) {
    Serial.print(readIntFromEEPROM(i)); // timestamp 2 bytes
    Serial.print("\t");
    Serial.print((char) EEPROM.read(i+2)); // Status 1 byte
    Serial.print("\t");
    Serial.print(readIntFromEEPROM(i+3)); // Altitude 2 bytes
    Serial.println();
  }
}
#endif

void lockParachuteSequence()
{
  // All led high servo open for parachute insertion
  digitalWrite(redLed, HIGH);
  digitalWrite(blueLed, HIGH);
  digitalWrite(greenLed, HIGH);
  servo.attach(pinApogee);
  servo.write(15);
  delay(8000);
  servo.write(40);
  // Leds off after servo lock
  digitalWrite(redLed, LOW);
  digitalWrite(blueLed, LOW);
  digitalWrite(greenLed, LOW);
}

void deployParachute()
{
  // 40 deg close
  // 15 deg Open
  if (apogeeHasFired == false)
  {
    servo.write(15);
    apogeeHasFired = true;
  }
}

void setup()
{
#if SERIAL_DEBUG
  Serial.begin(9600);
#endif

#if SERIAL_DEBUG
 eepromDataReader();
#endif

  Wire.begin();

  // LED pins
  pinMode(redLed, OUTPUT);
  pinMode(greenLed, OUTPUT);
  pinMode(blueLed, OUTPUT);
  pinMode(buzzer, OUTPUT);
  pinMode(intLed, OUTPUT);
  pinMode(pinApogee, OUTPUT);

  // Led / Buzzer test sequence
  digitalWrite(intLed, HIGH);
  delay(300);
  digitalWrite(redLed, HIGH);
  delay(300);
  digitalWrite(greenLed, HIGH);
  delay(300);
  digitalWrite(blueLed, HIGH);
  delay(300);
  digitalWrite(redLed, LOW);
  digitalWrite(blueLed, LOW);
  digitalWrite(greenLed, LOW);
  digitalWrite(intLed, LOW);

  // Buzzer test
  tone(buzzer, 440);
  delay(500);
  noTone(buzzer);

  // Modules Init and checks
  if (!SD.begin(10))
  {
#if SERIAL_DEBUG
    Serial.println("Card failed, or not present");
#endif
    status = 10;
  }
  else
  {
    root = SD.open("/");
    filename = getFileName(root, 0);
  }

  if (!bmp.begin(10))
  {
#if SERIAL_DEBUG
    Serial.println("BMP sensor failed!");
#endif
    status = 11;
  }

  // MPU Sensor Initialisation
  mpu.initialize();
  if (!mpu.testConnection())
  {
#if SERIAL_DEBUG
    Serial.println("MPU Failed!");
#endif
    // If it fails, it won't stop working
    // logs will not fetch MPU data
    // status = 12;
    useMPUData = false;
  }

  // Averagely measured P0
  float pressoureAccum = 0;
  for (int i = 0; i < 10; i++)
  {
    delay(10);
    pressoureAccum += bmp.readPressure();
  }

  P0 = pressoureAccum / 10;

  // Averagely measured Altitude
  float altitudeAccum = 0;
  for (int i = 0; i < 10; i++)
  {
    altitudeAccum += KalmanCalc(bmp.readAltitude(P0));
    delay(10);
  }
  initialAltitude = int(altitudeAccum / 10.0);

  // initialise the Kalman filter
  KalmanInit();
  for (int i = 0; i < 50; i++)
  {
    delay(10);
    KalmanCalc(bmp.readAltitude(P0));
  }

#if SERIAL_DEBUG
  Serial.println("P0 value: " + String(P0));
  Serial.println("Iniotial Altitude value: " + String(initialAltitude));
  Serial.println("Status: " + String(status));
#endif

  if (status == STATUS_READY)
  {
    lockParachuteSequence();
  }
  millisFromLastBlink = millisAtCurrentLoop;
}

void loop()
{
  // Unified time for the entire loop **millisAtCurrentLoop**
  if (millisAtLoopStart == 0) {
    millisAtLoopStart = millis();
  } else {
    millisAtCurrentLoop = millis() - millisAtLoopStart;
  }

  // Led status blink
  if (millisAtCurrentLoop - millisFromLastBlink >= 500)
  {
    statusMonitor();
    millisFromLastBlink = millisAtCurrentLoop;
  }

  // Skip all the above if its not ready or have landed
  if (status < STATUS_READY || status == STATUS_LANDED)
  {
    return;
  }
  
  rawTemp = bmp.readTemperature();
  rawAltitude = bmp.readAltitude(P0);
  currentLoopAltitude = KalmanCalc(rawAltitude) - initialAltitude;

#if SERIAL_DEBUG
  Serial.println("Runtime " + String(millisAtCurrentLoop));
  Serial.println("Raw Altitude " + String(rawAltitude));
  Serial.println("Kalman Altitude " + String(currentLoopAltitude));
  Serial.println("Previous Altitude: " + String(previousLoopAltitude));
  Serial.println("Raw Temp: " + String(rawTemp));
  Serial.println("Status: " + String(status));
#endif

  // Liftoff detection
  if (status == STATUS_READY && (currentLoopAltitude > initialAltitude + LIFTOFF_THRESHOLD))
  {
    status = STATUS_LIFTOFF;
    millisAtLiftoff = millisAtCurrentLoop;
  }

  // Apogee detection
  if (status == STATUS_LIFTOFF)
  {
    if (currentLoopAltitude > previousLoopAltitude)
    {
      consecutiveAltitudeDrop = APOGEE_THRESHOLD;
    }
    else
    {
      if (consecutiveAltitudeDrop == 0)
      {
        status = STATUS_APOGEE;
      }
      else
      {
        if (previousLoopAltitude != currentLoopAltitude)
        { 
          consecutiveAltitudeDrop -= 1;
        }
      }
    } 
    previousLoopAltitude = currentLoopAltitude;
  }

  // Deploy Parachute / Rescue secuence
  if (status >= STATUS_APOGEE)
  {
    // Eject nose cone with servo
    if (currentLoopAltitude < 100) {
      deployParachute();
    }
    
  }

  // Detect Landing
  // Simplyfy landed check
  // Just count 20 seconds after liftoff
  // This needs better computing, but this simplyfies it for now
  // [liftoff, ..]
  if (status >= STATUS_LIFTOFF)
  {
    if (millisAtCurrentLoop - millisAtLiftoff > 20000) {
      status = STATUS_LANDED;
    }
  }

  // Emergency parachute deployment [liftoff, landed)
  if (status >= STATUS_LIFTOFF && status < STATUS_LANDED)
  {
    if ((millisAtCurrentLoop - millisAtLiftoff) >= SECURITY_DEPLOYMENT_TIME)
    {
      deployParachute();
      status = STATUS_EMERGENCY_DEPLOY;
    }
  }

  // SD storage on whenever ready
  // code as is will only write 1 last log when landed
  sdDataLogger();
  // [liftoff, landed)
  if (status >= STATUS_LIFTOFF and status < STATUS_LANDED)
  {
    // To prevent damaging eeprom, only store important flight data 
    eepromDataLogger();
  }
}

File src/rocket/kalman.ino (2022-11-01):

/*================================================================
   Kalman functions in your code for Altimeter
   Kalman filter from Boris du Reau
  ================================================================
  Call KalmanInit() once
*/

// KalmanInit() - Call before any iterations of KalmanCalc()

//*********Kalman filter Variables*****************
float f_1 = 1.00000;
float kalman_x;
float kalman_x_last;
float kalman_p;
float kalman_p_last;
float kalman_k;
float kalman_q;
float kalman_r;
float kalman_x_temp;
float kalman_p_temp;

void KalmanInit()
{
  kalman_q = 4.0001; // filter parameters, you can play around with them
  kalman_r = .20001; // but these values appear to be fairly optimal

  kalman_x = 0;
  kalman_p = 0;
  kalman_x_temp = 0;
  kalman_p_temp = 0;

  kalman_x_last = 0;
  kalman_p_last = 0;
}

// KalmanCalc() - Calculates new Kalman values from float value "altitude"
//  This will be the ASL altitude during the flight, and the AGL altitude during dumps
float KalmanCalc(float altitude)
{

  // Predict kalman_x_temp, kalman_p_temp
  kalman_x_temp = kalman_x_last;
  kalman_p_temp = kalman_p_last + kalman_r;

  // Update kalman values
  kalman_k = (f_1 / (kalman_p_temp + kalman_q)) * kalman_p_temp;
  kalman_x = kalman_x_temp + (kalman_k * (altitude - kalman_x_temp));
  kalman_p = (f_1 - kalman_k) * kalman_p_temp;

  // Save this state for next time
  kalman_x_last = kalman_x;
  kalman_p_last = kalman_p;

  // Assign current Kalman filtered altitude to working variables
  // KAlt = kalman_x; //FLOAT Kalman-filtered altitude value
  return kalman_x;
}

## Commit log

2021-06-09 first working code
    [log.csv]
2021-06-09 play hastley
    [sketch.fzz, test.kicad_pcb, test.sch]
2021-06-09 remove test files
    [test.kicad_pcb, test.sch]
2021-06-10 working version 1
    [log_1.csv]
2021-06-11 remove some logs
    [log.csv, log_1.csv]
2021-06-16 servo updates
    [sketch.fzz]
2022-10-15 Fix apogee issues, removews MPU, improves python test apogee
    [sketch lite.fzz]
2022-10-15 bmp18 and apogee issues
    [sketch lite.fzz]
2022-10-25 Add MPU back, reduce memory usaga, better logs
    [log_fail.csv]
2022-10-29 init sequence to open then close servos
2022-11-01 Change servo angle from 0-25 to 15-45 to prevent servo heating. Refactor some code and use some macros for serial debbug
    [kalman.ino, rocket.ino]
2022-11-08 count millis at loop start
2022-11-08 python apogee util using eeprom format
    [log_eeprom.csv, log_fail.csv]
2022-11-08 inteval based landing detection
2022-11-10 Liftoff distance threshold, simple landing check
2023-03-06 upload rocket stls and motor simulation
2023-03-06 add missing payload styl
    [body_payload_area.stl]
2023-11-06 Change deploy to below 100 meters, update designs
    [body_motor_section.stl]
2023-12-18 Add accel sensor data to chart
